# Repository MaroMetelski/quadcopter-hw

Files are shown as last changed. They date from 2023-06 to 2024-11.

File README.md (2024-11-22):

# Quadcopter flight controller

Brushed DC motor quadcopter flight controller hardware.

Schematics, PCB images and productions files for each release can be found
in https://github.com/MaroMetelski/quadcopter-hw/releases/.

# Revisions

## V1.0

Initial version of the brushed motor flight controller. Main features:

- 30.5x30.5 mm form factor
- Powered with 1S 3.7V battery
- On-board 1S Li-Po charger
- STM32F303RE controller
- Support for 6-channel PWM or 1-channel SBus radio receiver
- BQ274441 fuel gauge
- LSM6DSO 6-axis IMU (accelerometer & gyroscope)

Links:
- [Schematic](https://github.com/MaroMetelski/quadcopter-hw/releases/download/v1.0/quadcopter_v1.0_schematic.pdf)

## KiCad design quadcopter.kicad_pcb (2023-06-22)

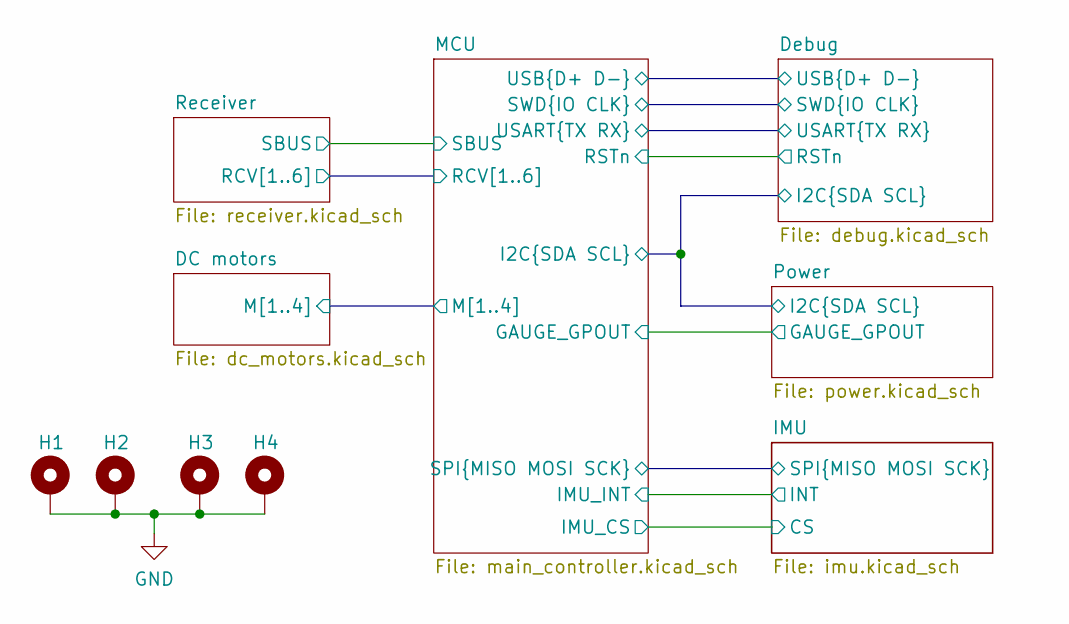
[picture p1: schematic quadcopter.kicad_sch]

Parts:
H1, H2, H3, H4: MountingHole_Pad; MountingHole_2.2mm_M2_Pad

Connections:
GND: H1.1, H2.1, H3.1, H4.1; also elsewhere on the board

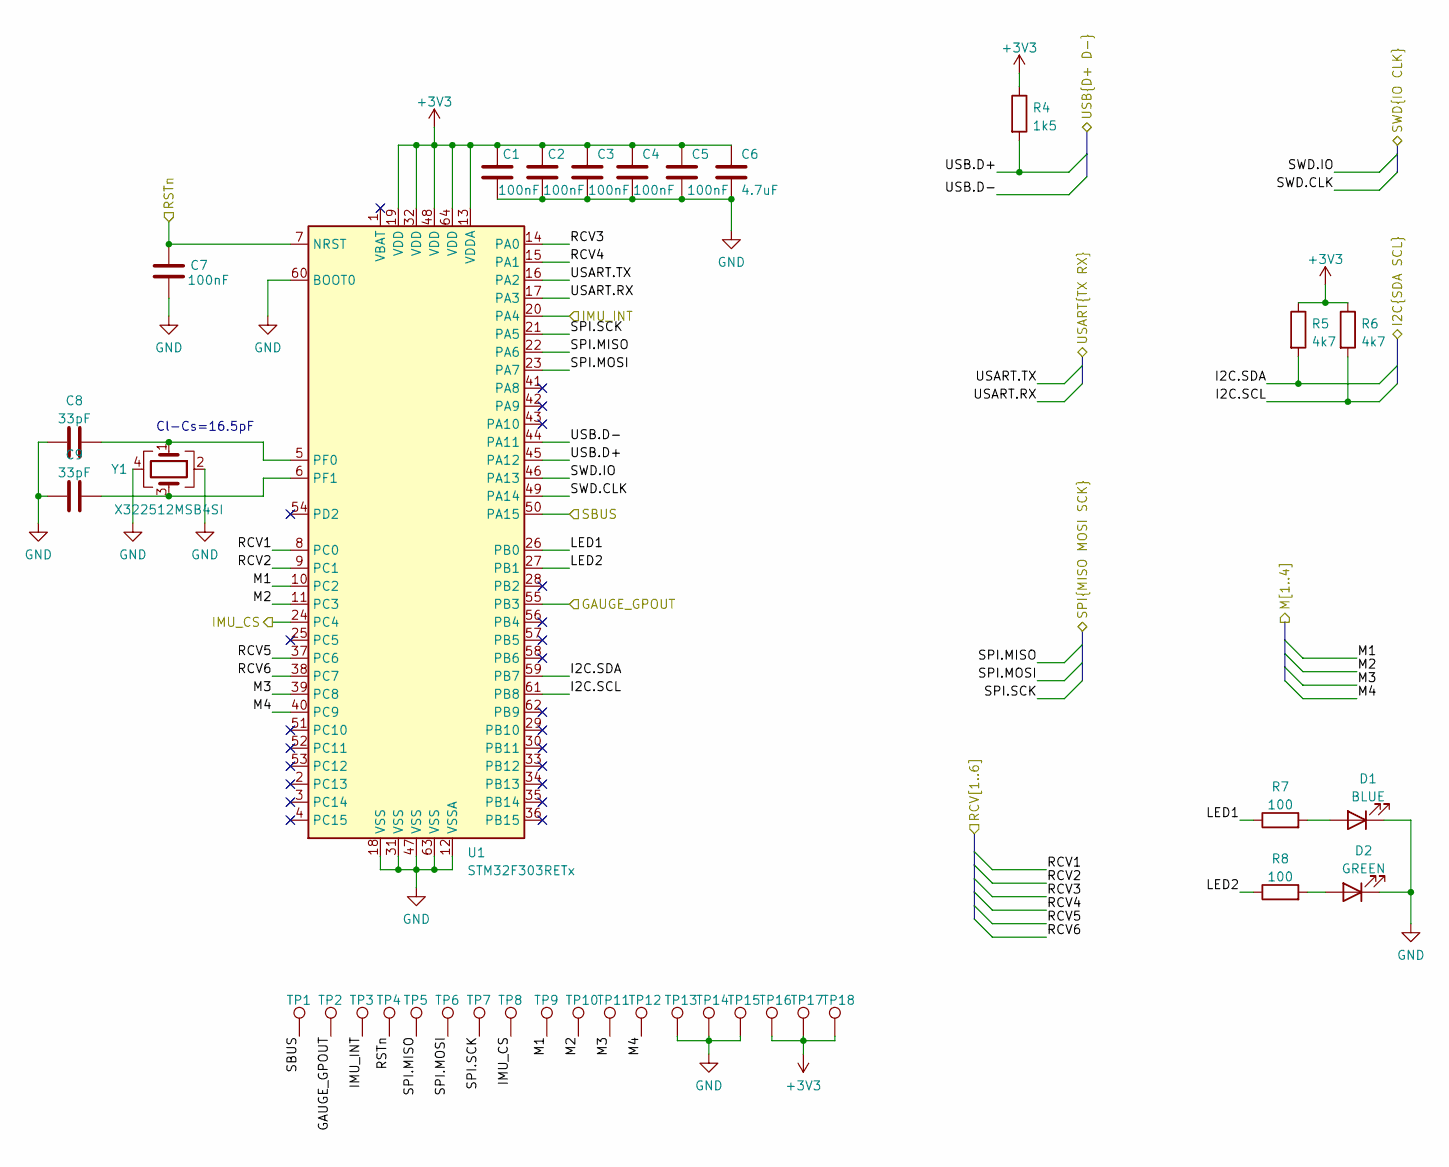
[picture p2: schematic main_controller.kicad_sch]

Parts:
C1, C2, C3, C4, C5, C7: 100nF; C_0402_1005Metric; JLC 0402
C6: 4.7uF; C_0402_1005Metric; JLC 0402
C8, C9: 33pF; C_0402_1005Metric; JLC 0402
D1: BLUE; LED_0603_1608Metric; JLC 0603
D2: GREEN; LED_0603_1608Metric; JLC 0603
R4: 1k5; R_0402_1005Metric; JLC 0402
R5, R6: 4k7; R_0402_1005Metric; JLC 0402
R7, R8: 100; R_0402_1005Metric; JLC 0402
TP1, TP2, TP3, TP4, TP5, TP6, TP7, TP8, TP9, TP10, TP11, TP12, TP13, TP14, TP15, TP16, TP17, TP18: TestPoint; TestPoint_Pad_D1.0mm
U1: STM32F303RETx; LQFP-64_10x10mm_P0.5mm; JLC LQFP-64(10x10)
Y1: X322512MSB4SI; Crystal_SMD_3225-4Pin_3.2x2.5mm; JLC SMD3225-4P

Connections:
+3V3: C1.1, C2.1, C3.1, C4.1, C5.1, C6.1, R4.1, R5.1, R6.1, TP16.1, TP17.1, TP18.1, U1.13 (VDDA), U1.19 (VDD), U1.32 (VDD), U1.48 (VDD), U1.64 (VDD); also elsewhere on the board
/DC motors/M1: TP9.1, U1.10 (PC2); also elsewhere on the board
/DC motors/M2: TP10.1, U1.11 (PC3); also elsewhere on the board
/DC motors/M3: TP11.1, U1.39 (PC8); also elsewhere on the board
/DC motors/M4: TP12.1, U1.40 (PC9); also elsewhere on the board
/Debug/I2C.SCL: R6.2, U1.61 (PB8); also elsewhere on the board
/Debug/I2C.SDA: R5.2, U1.59 (PB7); also elsewhere on the board
/Debug/SWD.CLK: U1.49 (PA14); also elsewhere on the board
/Debug/SWD.IO: U1.46 (PA13); also elsewhere on the board
/Debug/USART.RX: U1.17 (PA3); also elsewhere on the board
/Debug/USART.TX: U1.16 (PA2); also elsewhere on the board
/Debug/USB.D+: R4.2, U1.45 (PA12); also elsewhere on the board
/Debug/USB.D-: U1.44 (PA11); also elsewhere on the board
/IMU/SPI.MISO: TP5.1, U1.22 (PA6); also elsewhere on the board
/IMU/SPI.MOSI: TP6.1, U1.23 (PA7); also elsewhere on the board
/IMU/SPI.SCK: TP7.1, U1.21 (PA5); also elsewhere on the board
/MCU/GAUGE_GPOUT: TP2.1, U1.55 (PB3); also elsewhere on the board
/MCU/IMU_CS: TP8.1, U1.24 (PC4); also elsewhere on the board
/MCU/IMU_INT: TP3.1, U1.20 (PA4); also elsewhere on the board
/MCU/LED1: R7.1, U1.26 (PB0)
/MCU/LED2: R8.1, U1.27 (PB1)
/MCU/RCV1: U1.8 (PC0); also elsewhere on the board
/MCU/RCV2: U1.9 (PC1); also elsewhere on the board
/MCU/RCV3: U1.14 (PA0); also elsewhere on the board
/MCU/RCV4: U1.15 (PA1); also elsewhere on the board
/MCU/RCV5: U1.37 (PC6); also elsewhere on the board
/MCU/RCV6: U1.38 (PC7); also elsewhere on the board
/MCU/RSTn: C7.1, TP4.1, U1.7 (NRST); also elsewhere on the board
/MCU/SBUS: TP1.1, U1.50 (PA15); also elsewhere on the board
GND: C1.2, C2.2, C3.2, C4.2, C5.2, C6.2, C7.2, C8.1, C9.1, D1.1 (K), D2.1 (K), TP13.1, TP14.1, TP15.1, U1.12 (VSSA), U1.18 (VSS), U1.31 (VSS), U1.47 (VSS), U1.60 (BOOT0), U1.63 (VSS), Y1.2, Y1.4; also elsewhere on the board
unnamed: C8.2, U1.5 (PF0), Y1.1
unnamed: C9.2, U1.6 (PF1), Y1.3
unnamed: D1.2 (A), R7.2
unnamed: D2.2 (A), R8.2

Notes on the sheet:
Cl-Cs=16.5pF

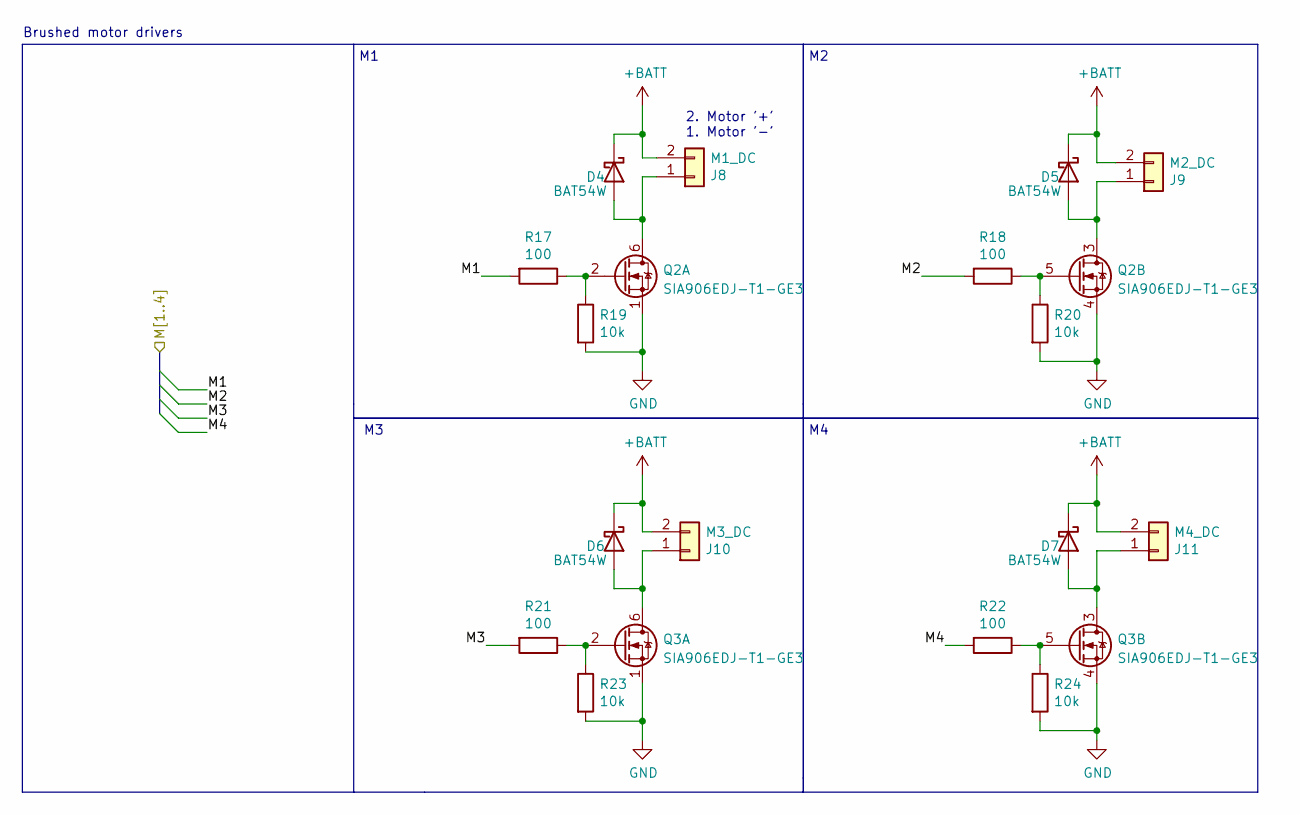
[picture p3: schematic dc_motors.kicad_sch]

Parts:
D4, D5, D6, D7: BAT54W; D_SOD-123; LCSC C915628
J8: M1_DC; PinHeader_1x02_P2.54mm_Vertical
J9: M2_DC; PinHeader_1x02_P2.54mm_Vertical
J10: M3_DC; PinHeader_1x02_P2.54mm_Vertical
J11: M4_DC; PinHeader_1x02_P2.54mm_Vertical
Q2, Q3: SIA906EDJ-T1-GE3; Vishay_PowerPAK_SC70-6L_Dual; JLC WSON-6-EP(2x2)
R17, R18, R21, R22: 100; R_0402_1005Metric; JLC 0402
R19, R20, R23, R24: 10k; R_0402_1005Metric; JLC 0402

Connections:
+BATT: D4.1 (K), D5.1 (K), D6.1 (K), D7.1 (K), J8.2, J9.2, J10.2, J11.2; also elsewhere on the board
/DC motors/M1: R17.2; also elsewhere on the board
/DC motors/M2: R18.2; also elsewhere on the board
/DC motors/M3: R21.2; also elsewhere on the board
/DC motors/M4: R22.2; also elsewhere on the board
GND: Q2.1 (S), Q2.4 (S), Q3.1 (S), Q3.4 (S), R19.2, R20.2, R23.2, R24.2; also elsewhere on the board
unnamed: D4.2 (A), J8.1, Q2.6 (D)
unnamed: D5.2 (A), J9.1, Q2.3 (D)
unnamed: D6.2 (A), J10.1, Q3.6 (D)
unnamed: D7.2 (A), J11.1, Q3.3 (D)
unnamed: Q2.2 (G), R17.1, R19.1
unnamed: Q2.5 (G), R18.1, R20.1
unnamed: Q3.2 (G), R21.1, R23.1
unnamed: Q3.5 (G), R22.1, R24.1

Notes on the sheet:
2. Motor '+' 1. Motor '-'
Brushed motor drivers

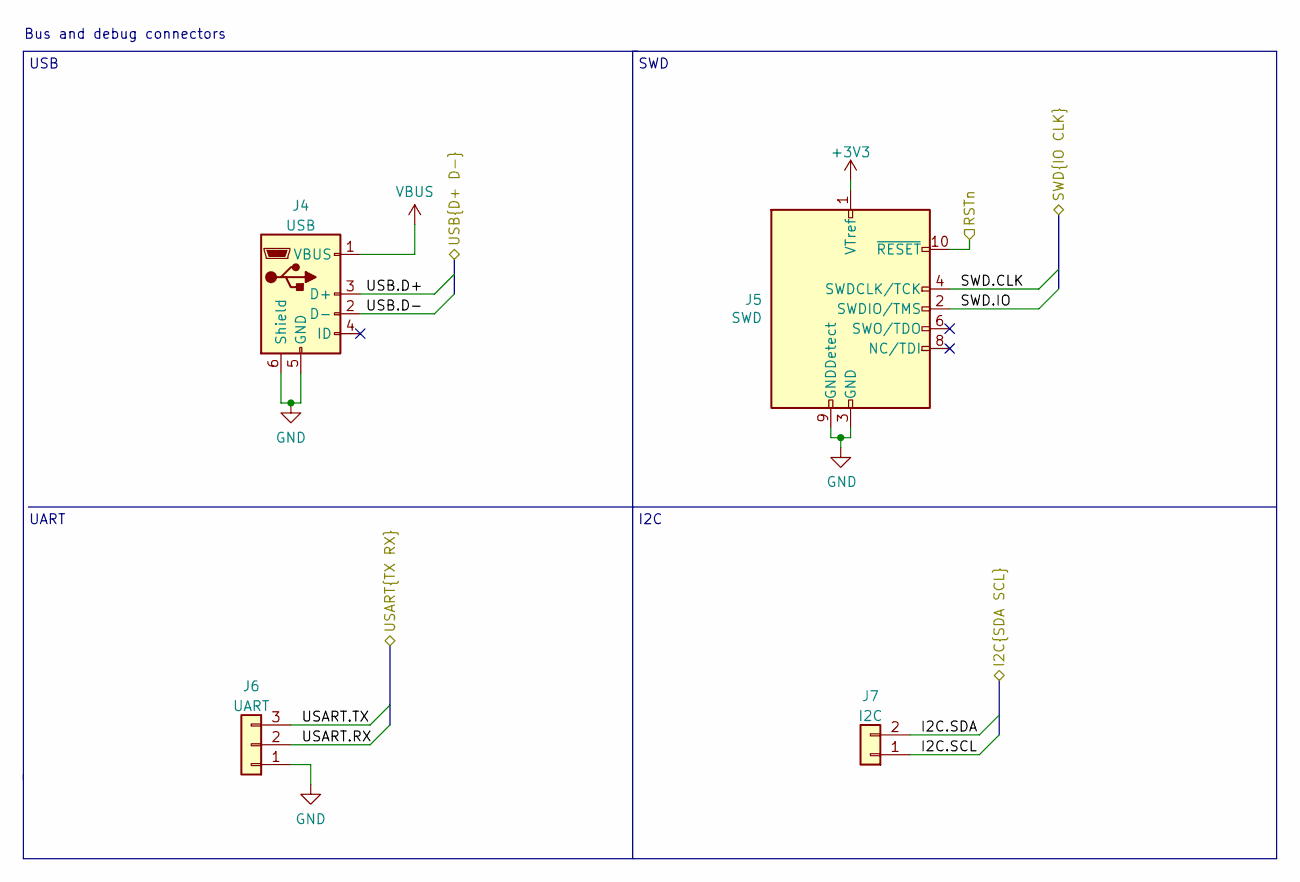
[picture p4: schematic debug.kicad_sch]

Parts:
J4: USB; USB_Micro-B_Molex-105017-0001; JLC SMD
J5: SWD; PinHeader_2x05_P1.27mm_Vertical_SMD
J6: UART; PinHeader_1x03_P2.54mm_Vertical
J7: I2C; PinHeader_1x02_P2.54mm_Vertical

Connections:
+3V3: J5.1 (VTref); also elsewhere on the board
/Debug/I2C.SCL: J7.1; also elsewhere on the board
/Debug/I2C.SDA: J7.2; also elsewhere on the board
/Debug/SWD.CLK: J5.4 (SWDCLK/TCK); also elsewhere on the board
/Debug/SWD.IO: J5.2 (SWDIO/TMS); also elsewhere on the board
/Debug/USART.RX: J6.2; also elsewhere on the board
/Debug/USART.TX: J6.3; also elsewhere on the board
/Debug/USB.D+: J4.3 (D+); also elsewhere on the board
/Debug/USB.D-: J4.2 (D-); also elsewhere on the board
/MCU/RSTn: J5.10 (~RESET); also elsewhere on the board
GND: J4.5 (GND), J4.6 (Shield), J5.3 (GND), J5.5 (GND), J5.9 (GNDDetect), J6.1; also elsewhere on the board
VBUS: J4.1 (VBUS); also elsewhere on the board

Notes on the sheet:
Bus and debug connectors
UART
I2C
USB
SWD

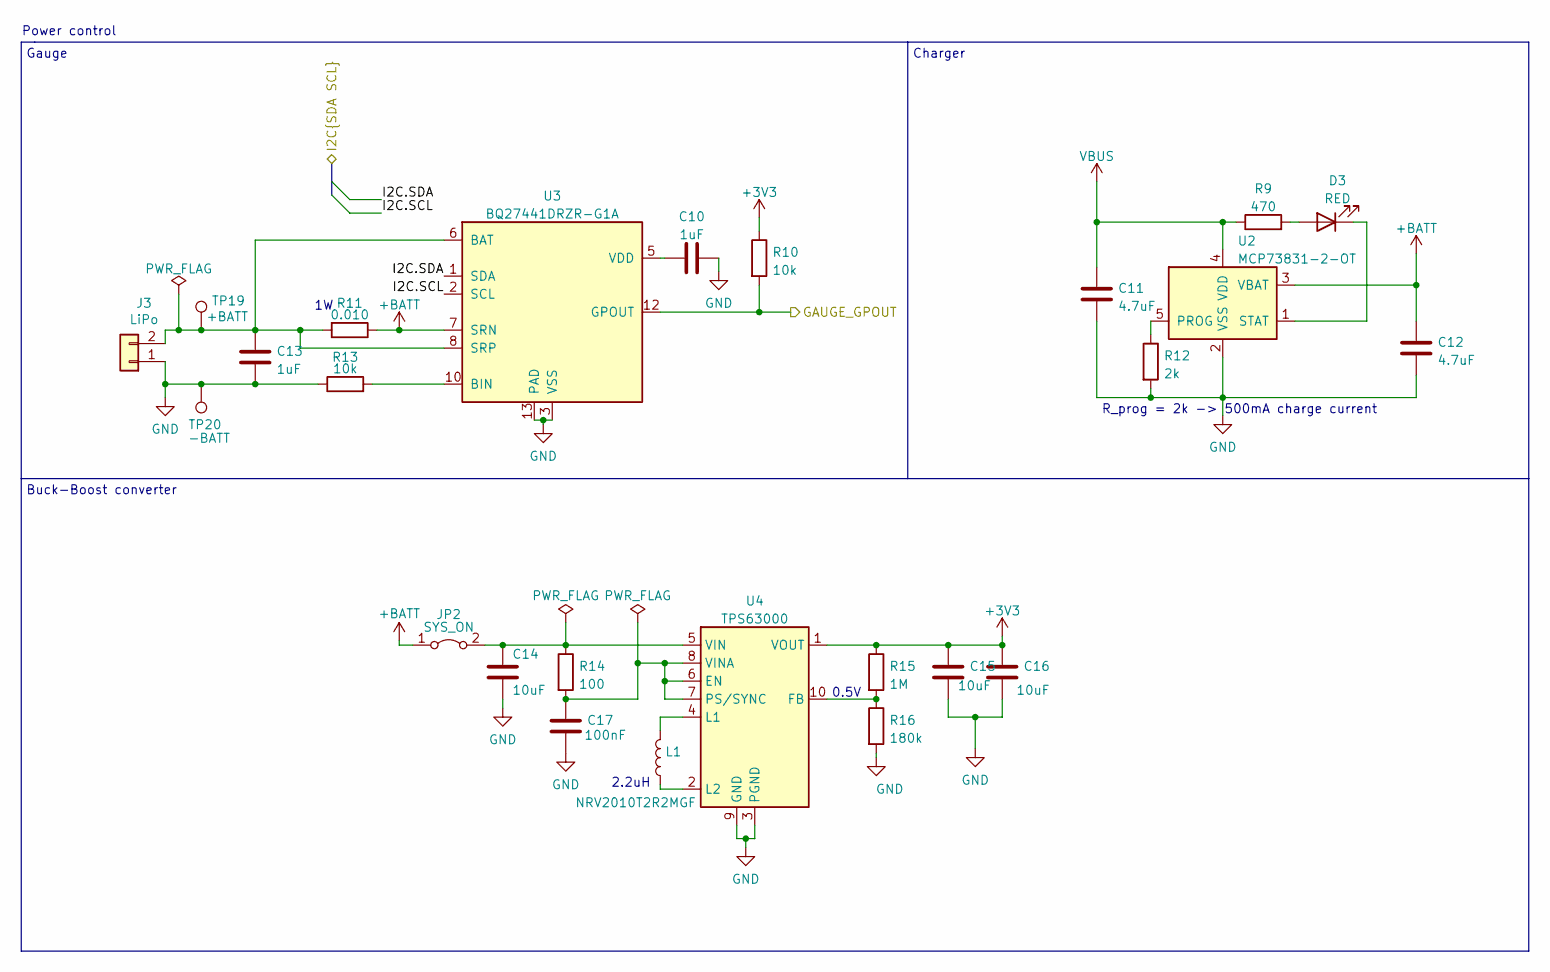
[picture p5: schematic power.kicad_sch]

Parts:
C10, C13: 1uF; C_0402_1005Metric; JLC 0402
C11, C12: 4.7uF; C_0402_1005Metric; JLC 0402
C14, C15, C16: 10uF; C_0402_1005Metric; JLC 0402
C17: 100nF; C_0402_1005Metric; JLC 0402
D3: RED; LED_0603_1608Metric; JLC 0603
J3: LiPo; PinHeader_1x02_P2.54mm_Vertical
JP2: SYS_ON; PinHeader_1x02_P2.54mm_Vertical
L1: NRV2010T2R2MGF; L_Taiyo-Yuden_NR-20xx; JLC SMD
R9: 470; R_0402_1005Metric; JLC 0402
R10, R13: 10k; R_0402_1005Metric; JLC 0402
R11: 0.010; R_2010_5025Metric; JLC 2010
R12: 2k; R_0402_1005Metric; JLC 0402
R14: 100; R_0402_1005Metric; JLC 0402
R15: 1M; R_0402_1005Metric; JLC 0402
R16: 180k; R_0402_1005Metric; JLC 0402
TP19: +BATT; TestPoint_Pad_2.0x2.0mm
TP20: -BATT; TestPoint_Pad_2.0x2.0mm
U2: MCP73831-2-OT; SOT-23-5; JLC SOT-23-5
U3: BQ27441DRZR-G1A; Texas_S-PDSO-N12; JLC SON-12-EP(2.5x4)
U4: TPS63000; Texas_DRC0010J_ThermalVias; JLC SON-10-EP(3.1x3.1)

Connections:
+3V3: C15.1, C16.1, R10.1, R15.1, U4.1 (VOUT); also elsewhere on the board
+BATT: C12.1, JP2.1 (A), R11.1, U2.3 (VBAT), U3.7 (SRN); also elsewhere on the board
/Debug/I2C.SCL: U3.2 (SCL); also elsewhere on the board
/Debug/I2C.SDA: U3.1 (SDA); also elsewhere on the board
/MCU/GAUGE_GPOUT: R10.2, U3.12 (GPOUT); also elsewhere on the board
GND: C10.2, C11.2, C12.2, C13.2, C14.2, C15.2, C16.2, C17.2, J3.1, R12.2, R13.1, R16.2, TP20.1, U2.2 (VSS), U3.3 (VSS), U3.13 (PAD), U4.3 (PGND), U4.9 (GND), U4.11 (PGND); also elsewhere on the board
unnamed: C10.1, U3.5 (VDD)
unnamed: C13.1, J3.2, R11.2, TP19.1, U3.6 (BAT), U3.8 (SRP)
unnamed: C14.1, JP2.2 (B), R14.1, U4.5 (VIN)
unnamed: C17.1, R14.2, U4.6 (EN), U4.7 (PS/SYNC), U4.8 (VINA)
unnamed: D3.1 (K), U2.1 (STAT)
unnamed: D3.2 (A), R9.2
unnamed: L1.1, U4.2 (L2)
unnamed: L1.2, U4.4 (L1)
unnamed: R12.1, U2.5 (PROG)
unnamed: R13.2, U3.10 (BIN)
unnamed: R15.2, R16.1, U4.10 (FB)
VBUS: C11.1, R9.1, U2.4 (VDD); also elsewhere on the board

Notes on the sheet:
2.2uH
Charger
R_prog = 2k -> 500mA charge current
Gauge
Power control
Buck-Boost converter
0.5V

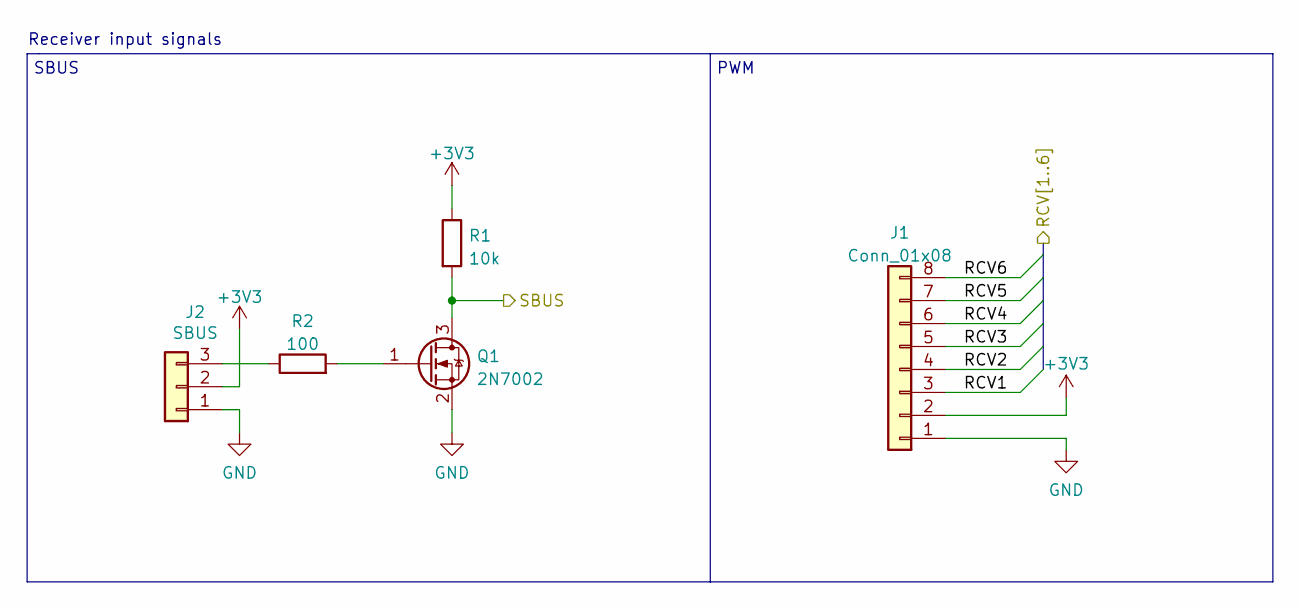
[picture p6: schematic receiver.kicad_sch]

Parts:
J1: Conn_01x08; PinHeader_1x08_P2.54mm_Vertical
J2: SBUS; PinHeader_1x03_P2.54mm_Vertical
Q1: 2N7002; SOT-23; JLC SOT-23
R1: 10k; R_0402_1005Metric; JLC 0402
R2: 100; R_0402_1005Metric; JLC 0402

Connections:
+3V3: J1.2, J2.2, R1.1; also elsewhere on the board
/MCU/RCV1: J1.3; also elsewhere on the board
/MCU/RCV2: J1.4; also elsewhere on the board
/MCU/RCV3: J1.5; also elsewhere on the board
/MCU/RCV4: J1.6; also elsewhere on the board
/MCU/RCV5: J1.7; also elsewhere on the board
/MCU/RCV6: J1.8; also elsewhere on the board
/MCU/SBUS: Q1.3 (D), R1.2; also elsewhere on the board
GND: J1.1, J2.1, Q1.2 (S); also elsewhere on the board
unnamed: J2.3, R2.1
unnamed: Q1.1 (G), R2.2

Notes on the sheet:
Receiver input signals
PWM
SBUS

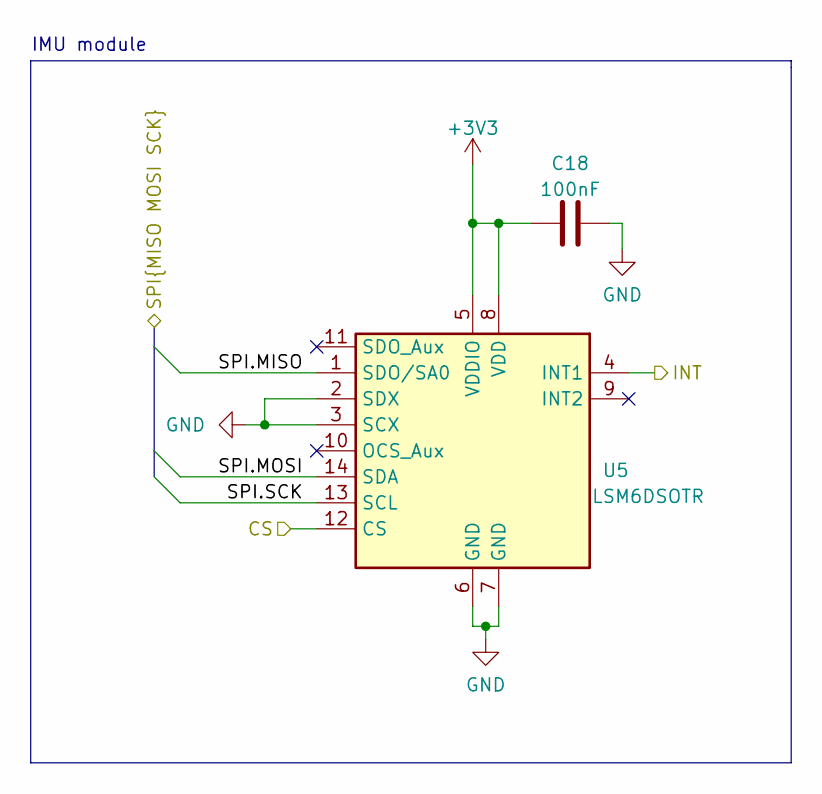
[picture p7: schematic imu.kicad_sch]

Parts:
C18: 100nF; C_0402_1005Metric; JLC 0402
U5: LSM6DSOTR; LGA-14_3x2.5mm_P0.5mm_LayoutBorder3x4y; JLC LGA-14(2.5x3)

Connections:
+3V3: C18.2, U5.5 (VDDIO), U5.8 (VDD); also elsewhere on the board
/IMU/SPI.MISO: U5.1 (SDO/SA0); also elsewhere on the board
/IMU/SPI.MOSI: U5.14 (SDA); also elsewhere on the board
/IMU/SPI.SCK: U5.13 (SCL); also elsewhere on the board
/MCU/IMU_CS: U5.12 (CS); also elsewhere on the board
/MCU/IMU_INT: U5.4 (INT1); also elsewhere on the board
GND: C18.1, U5.2 (SDX), U5.3 (SCX), U5.6 (GND), U5.7 (GND); also elsewhere on the board

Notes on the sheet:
IMU module

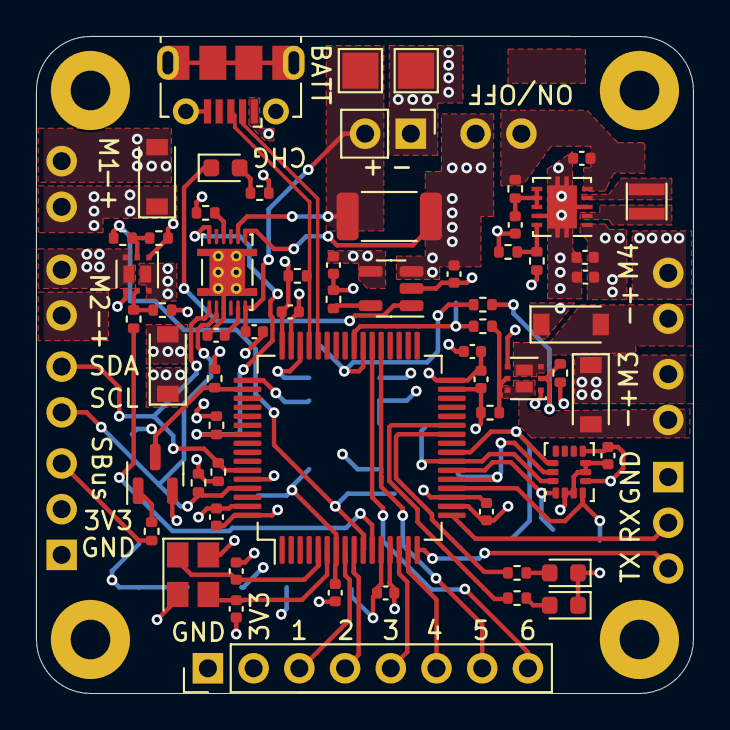
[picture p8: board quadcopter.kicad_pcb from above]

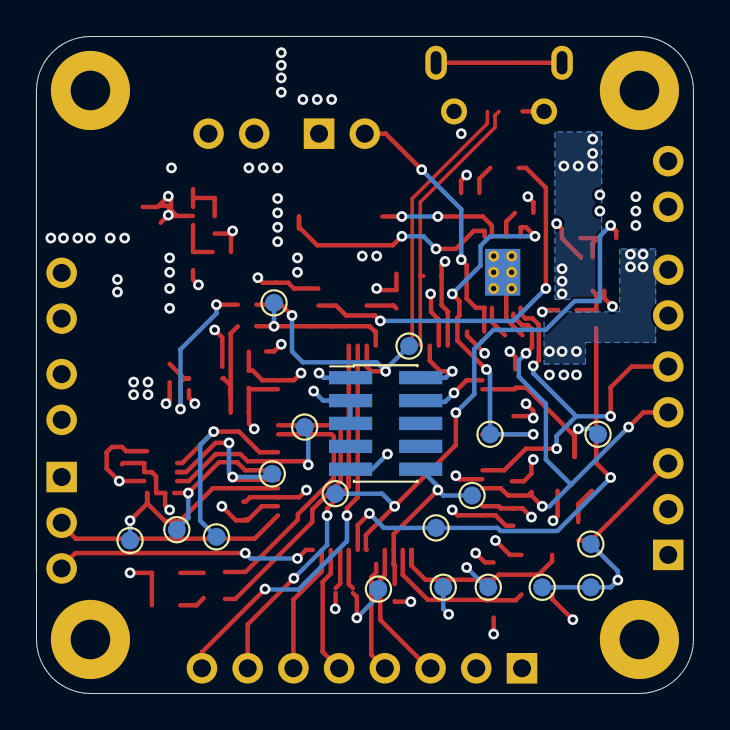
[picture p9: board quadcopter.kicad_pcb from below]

Board: 4 copper layers, 36.5 x 36.5 mm, 94 parts (19 on the bottom side), 57 nets.

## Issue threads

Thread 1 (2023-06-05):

Schematic Review

MaroMetelski, 2023-06-05:
Double check the schematics for errors. Check reference designs for each part.
Check pin assignments.

# MCU
- [ ] MCU pin assignments wth datasheet
- [ ] MCU crystal
- [ ] nRST and BOOT pins
- [ ] Vcc and GND

# IMU
- [ ] connections & reference design

# Gauge
- [ ] connections & reference design

# Charger
- [ ] Loading current. Reference design

# Buck-boost
- [ ] Parameters. Voltage divider. Reference design

# Debug outputs
- [ ] I2C
- [ ] UART
- [ ] SWD
- [ ] Test pads for all other important signals.

# Motors
- [ ] mosfet driver correctness. mosfet specs

# Receivers
- [ ] Verify inverter design
- [ ] Verify receiver inputs

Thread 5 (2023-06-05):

Design PCB

MaroMetelski, 2023-06-05:
Design PCB
- v1.0 marking
- dimensions 30.5x30.5mm between holes
- 4 layers
- No components on bottom layer

Closed 2023-06-22.

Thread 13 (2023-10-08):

Add JLCPCB instructions

MaroMetelski, 2023-10-08:
Add instructions how to order the board with JLCPCB.
Add picture on how to rotate the components correctly.

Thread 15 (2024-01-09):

SBus not connected to UART_RX pin

MaroMetelski, 2024-01-09:
SBus signal is connected to a pin that is not available as free UART RX pin (PA15). The pin can function as UART2 RX but this is reserved for console UART.
A workaround is to solder a bridge to some other pin that offers other UART RX functionality, e.g. PC11.

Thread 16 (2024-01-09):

Change v1.x mounting pattern to 25.5x25.5mm.

MaroMetelski, 2024-01-09:
Most whoop frames that are suitable for brushed DC motor drones are compatible with 25.5mm boards.

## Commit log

2023-06-05 Initial schematic version
    This is now a clean and ready version of the schematic:
    That means:
    - Schematic has been reviewed,
    - It's fully annotated,
    - All elements have been checked for availability with JLCPCB,
    - Footprints were assigned,
    - ERC is green.
    No design changes should be added for this version until
    the PCB is present and version is released.
    Only bugfixes are possible now.
    [dc_motors.kicad_sch, debug.kicad_sch, flight_controller_v2.kicad_sch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]
2023-06-05 Update footprints and add JLCPCB fields
    Update some footprints which will suit better building the pcb
    with JLCBPCB. Add fields to components sourced from JLCPCB
    to be able to generate BOM.
    [dc_motors.kicad_sch, debug.kicad_sch, flight_controller_v2.kicad_sch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]
2023-06-05 Genarate JLCPCB BOM
    Add BOM compatible with JLCPCB. This allows to already check and / or
    source all the components.
    The BOM was generated using this script:
    https://github.com/djmdjm/KiJLC
    A modification was needed to change board.GetModules() to
    board.Footprints() in the script.
    See: https://github.com/NilujePerchut/kicad_scripts/issues/42
    [flight_controller_v2_bom_bot.csv, flight_controller_v2_bom_top.csv]
2023-06-05 Rename project to 'quadcopter'
    'flight_controller_v2' was the code name for the project based
    on the fact that there was a development version 'v1' of the PCB
    designed in Eagle which was not really mature. Except for the idea
    this is a completely new project - KiCAD, different components etc.
    Use generic name 'quadcopter' for now until the projects grows
    to an actual product.
    [quadcopter.kicad_sch, quadcopter_bom_bot.csv, quadcopter_bom_top.csv]
2023-06-05 fix: Fix D4-D7 schottky mismatch between symbol and footprint
    Symbol was placed for diode in SOT-323 package with 3 pins, but
    2 pin footprint was assigned. Use generic symbol with two pins.
    [dc_motors.kicad_sch, debug.kicad_sch, quadcopter.kicad_sch]
2023-06-22 Add finished PCB design for initial release
    This is quite a messy version of the initial PCB, hopefully without
    errors. Should conform to JLCPCB manufacturing process.
    This is a 4 layer PCB with components on the TOP, test pads and
    placement for debug connector on the bottom.
    The inside layers consist of a ground plane and a layer for power
    signals, especially 3v3 and BATT.
    [main_controller.kicad_sch, quadcopter.kicad_pcb, quadcopter.kicad_sch]
2023-06-22 Delete BOM files
    BOM files will be a part of the release package.
    [quadcopter_bom_bot.csv, quadcopter_bom_top.csv]
